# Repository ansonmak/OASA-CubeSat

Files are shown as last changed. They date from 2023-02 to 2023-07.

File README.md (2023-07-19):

# OASA-CubeSat Version 2.1
<p align = "center">
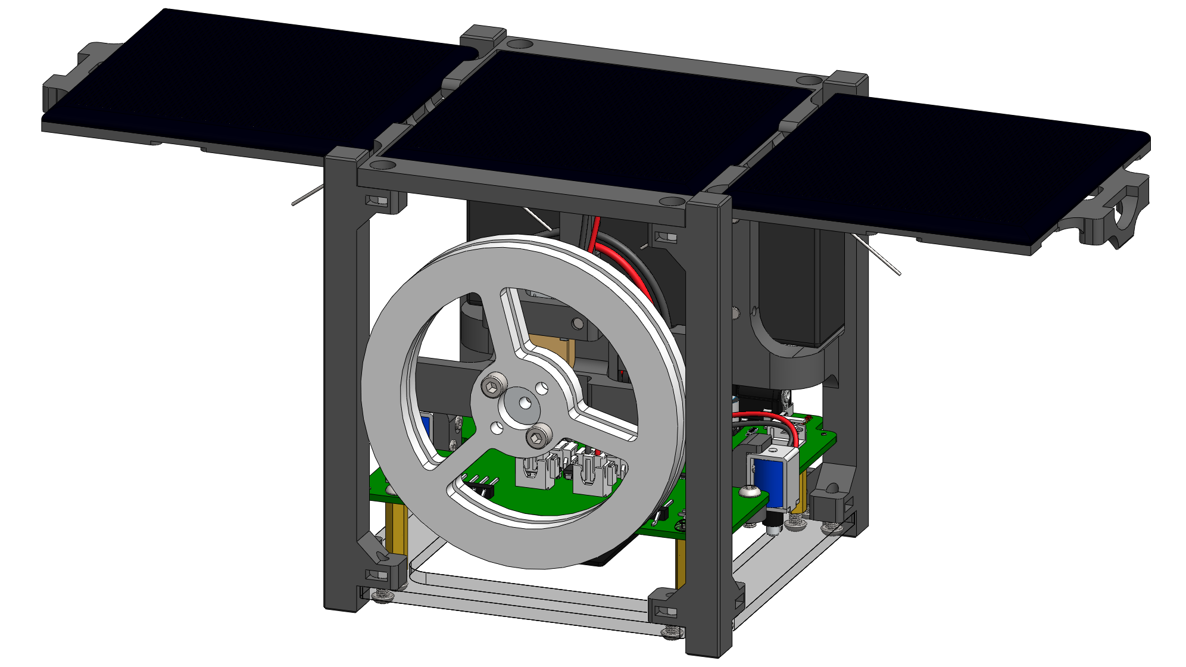
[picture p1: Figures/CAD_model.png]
 
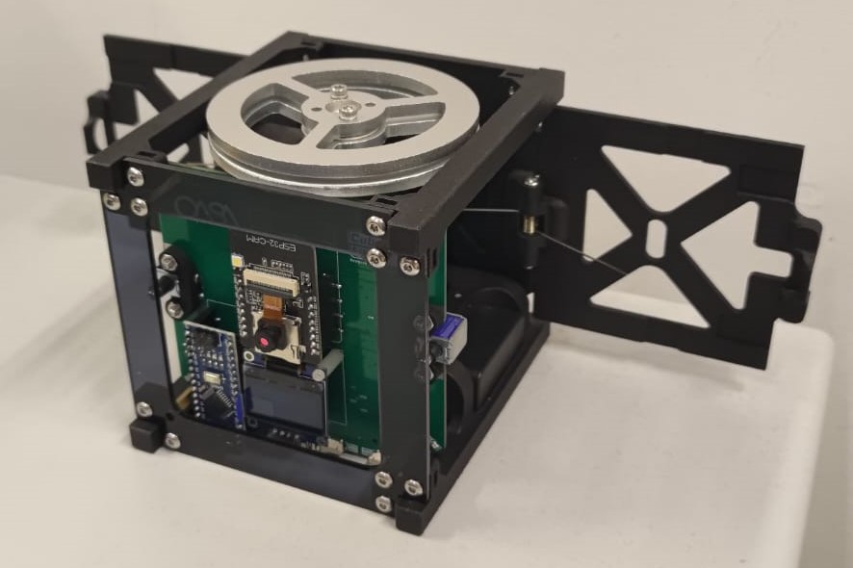
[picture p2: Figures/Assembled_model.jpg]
 
</p>

## 1. Overview
OASA-CubeSat is an educational satellite designed to imitate the most stucture and functions of a CubeSat, which is a cubic miniature satellite with the size of 10x10x10cm. This CubeSat is a double 18650 batteries powered device controlled by two microcontrollers: Arduino Nano and ESP32-CAM. It consists of one 12V geared DC motor for rotating the reaction wheel and two 5V solenoid actuators for deploying the solar panels. The CubeSat also contains a camera with a maximum resolution of 1600 x 1200. With our software uploaded to the microcontrollers, the camera's live-feed is able to transmit to and view it on the PC through its connected WiFi network. The electronics are all connected through our custom PCB mainboard which is attached within the CubeSat’s 3D printed structure.

This repository contains the instructions of how to assemble the CubeSat, guidelines of how to upload the included source code to the CubeSat, and the STL files of the 3D printed parts for replacement of the broken parts or customization.  

## 2. Assembly
Before assembling the CubeSat, check if anything in the kit is missing with the list below: 
- [OASA-CubeSat Kit Checklist](Docs/Checklist.md)

To assemble the CubeSat, follow the instructions below:
- [CubeSat Assembly Instruction](Docs/Assembly.md)

For printing the 3D printed parts with your own printer, check out the STL files in the [`STL`](STL/) to load the 3D models in your slicer.

## 3. Software
The source code of this CubeSat is located in the folder: [`Software`](Software/). Follow the tutorial below to see how to upload the software and operate the CubeSat:
- [Software Upload and CubeSat Operation](Docs/Software.md)

## 4. Copyright
**Copyright © 2023 Orion Astropreneur Space Academy (Hong Kong) Ltd.** 

The intellectual property of this educational CubeSat belongs to Orion Astropreneur Space Academy (Hong Kong) Ltd. All rights reserved.

## 5. Maintenance
For any technical issues, please contact Anson Mak with ansonmak1997@gmail.com.

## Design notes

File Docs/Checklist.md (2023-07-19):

# CubeSat Kit Checklist
- ## Parts
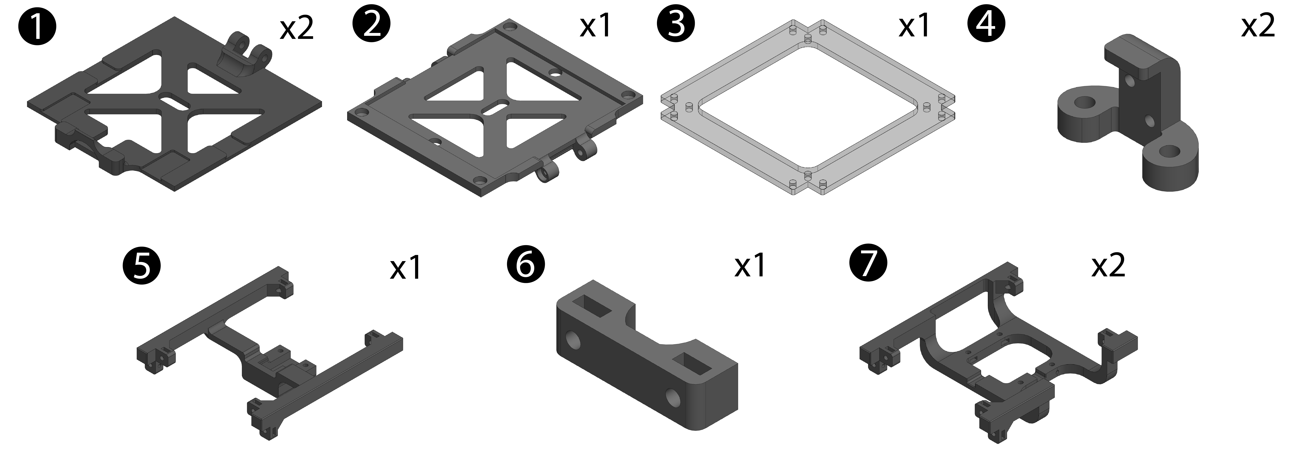
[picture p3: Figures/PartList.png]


- ## Components Box
    - Components of each cell in the box:

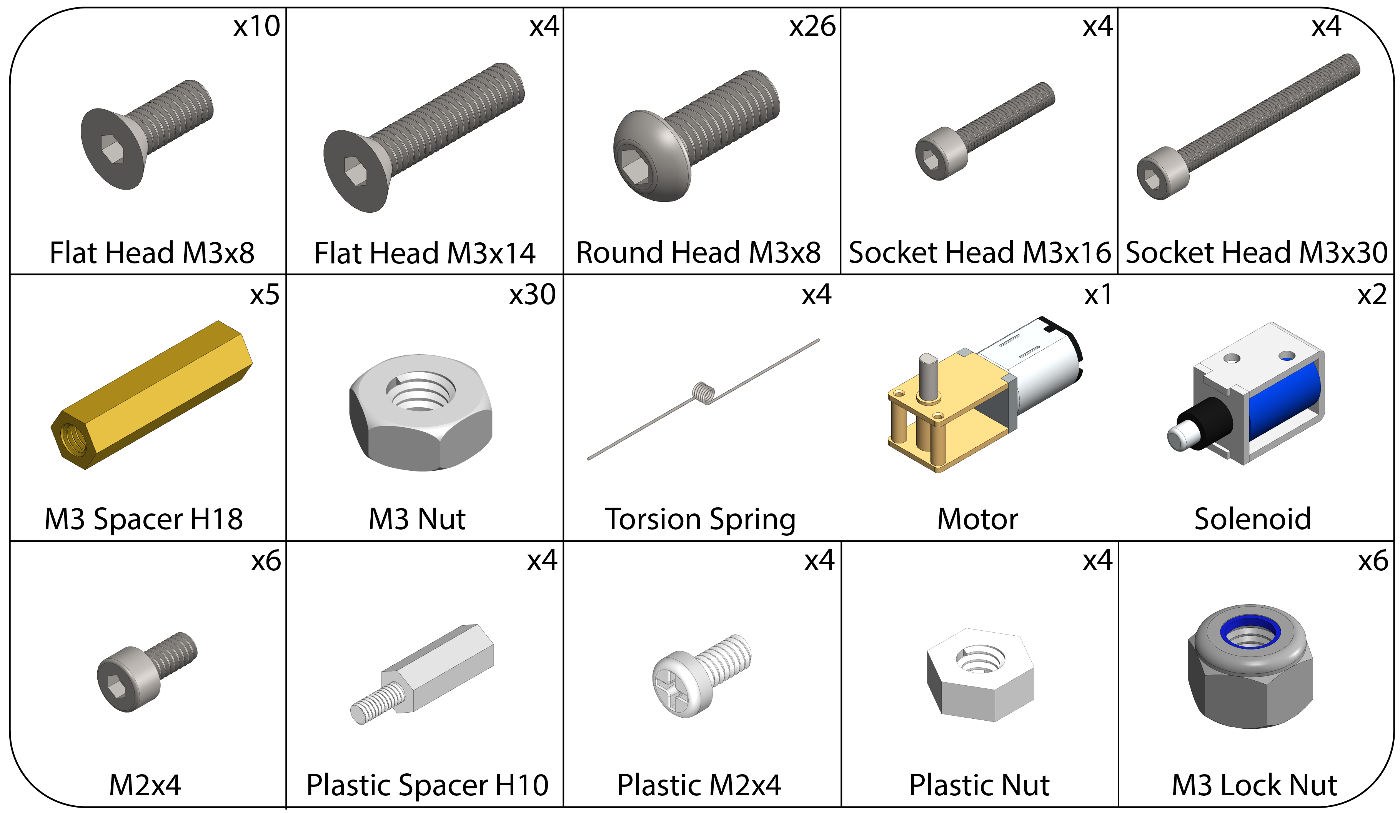
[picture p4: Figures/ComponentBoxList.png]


- ## Electronics
    - ### Mainboard
    - ### ESP32-CAM
    - ### Arduino Nano
    - ### OLED Display

- ## Tools Set
    - ### Hex Key: 1.5mm, 2.0mm, and 2.5mm
    - ### Mini Cross Screwdriver
    - ### Wrench: 5.5mm

- ## Solar Panel x 3

- ## Reaction Wheel Parts

- ## Battery 18650 cell x 2

- ## Battery USB Charger

- ## Battery Power Box

- ## Light Sensor With Wire and Header x 4

- ## Mini USB Wire

- ## Spare 3D Printed Parts

- ## Double Sided Tapes

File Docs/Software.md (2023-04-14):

# Software Tutorial

## 1. Install Arduino IDE
Visit https://www.arduino.cc/en/software to download and install Arduino IDE software on your computer.

## 2. Install ESP32 Board in Arduino IDE
After you have installed Arduino IDE on your computer, you will need to install the ESP32 board library in Arduino IDE before uploading code to the ESP32 board. 

**2.1** Launch Arduino IDE and go to **Files** > **Preferences**.  
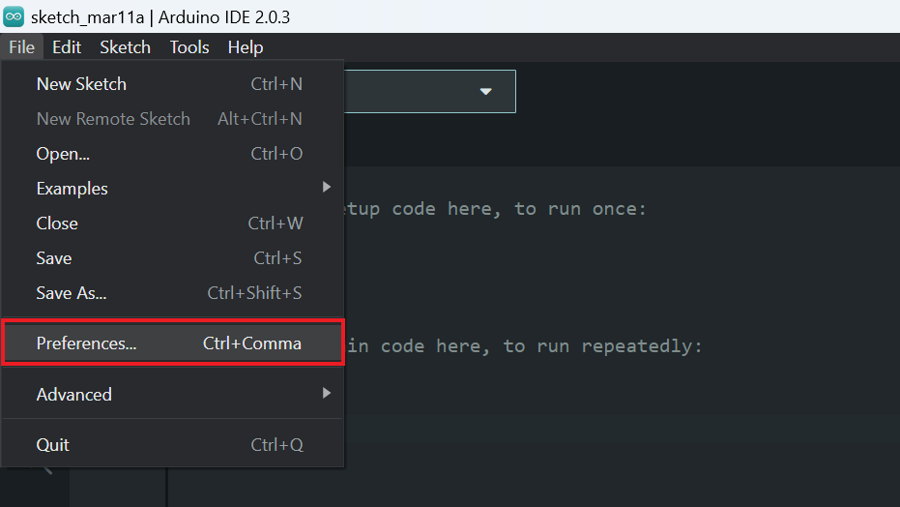
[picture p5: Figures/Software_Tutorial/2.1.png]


**2.2** In **Additional Boards Manager URLs**, paste the following link:
```
https://raw.githubusercontent.com/espressif/arduino-esp32/gh-pages/package_esp32_index.json
```  
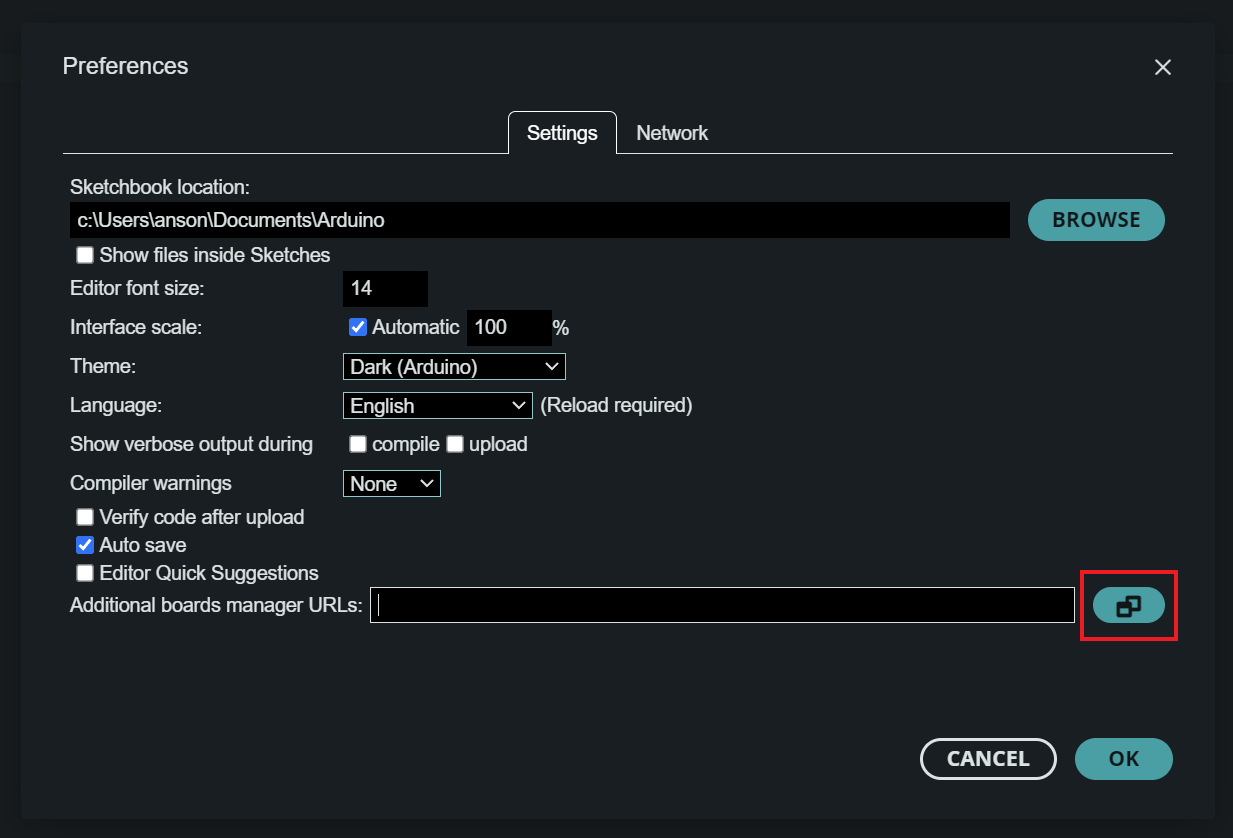
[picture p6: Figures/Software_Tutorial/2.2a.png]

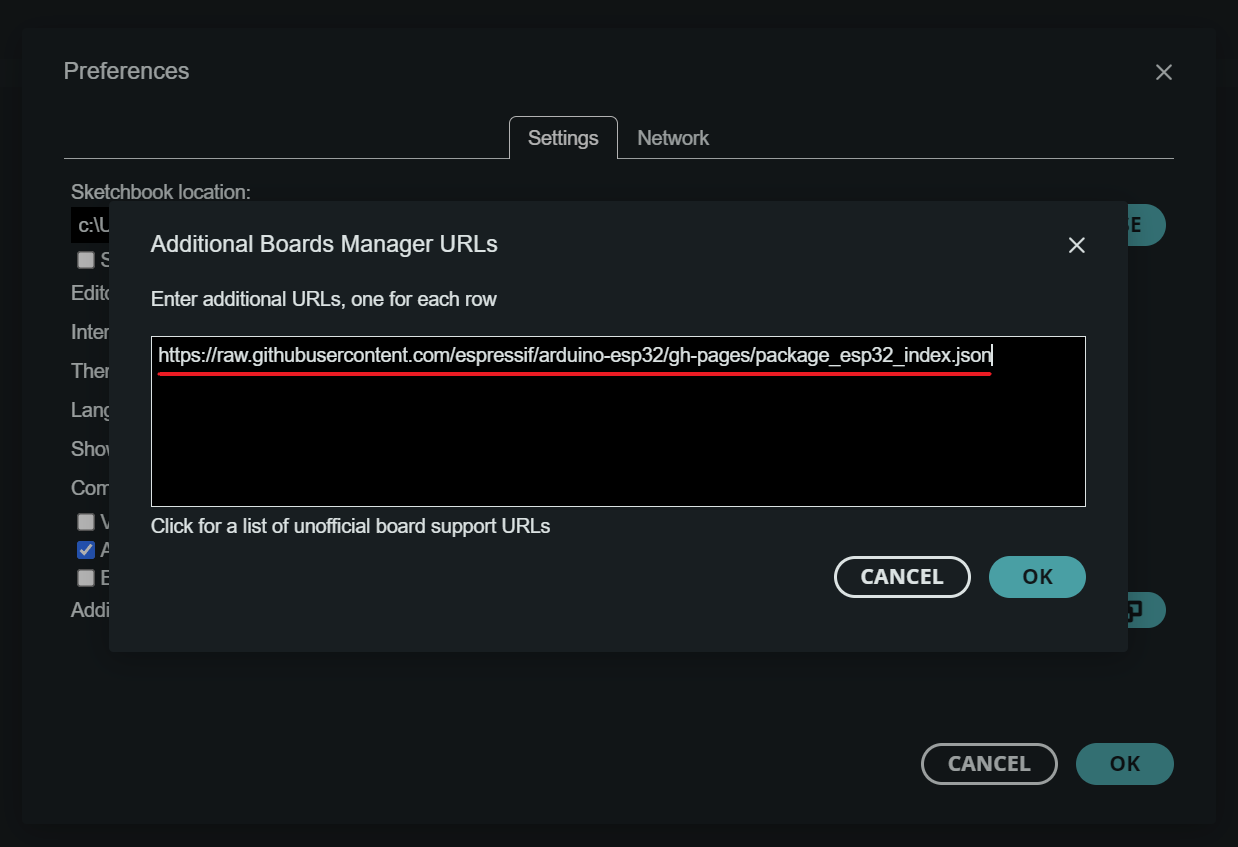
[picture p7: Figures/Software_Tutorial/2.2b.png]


**2.3** In **Tools** > **Board** > **Boards Manager** or click the **Boards Manager** icon on the left bar, search **ESP32** and install with **version 1.0.6**.  
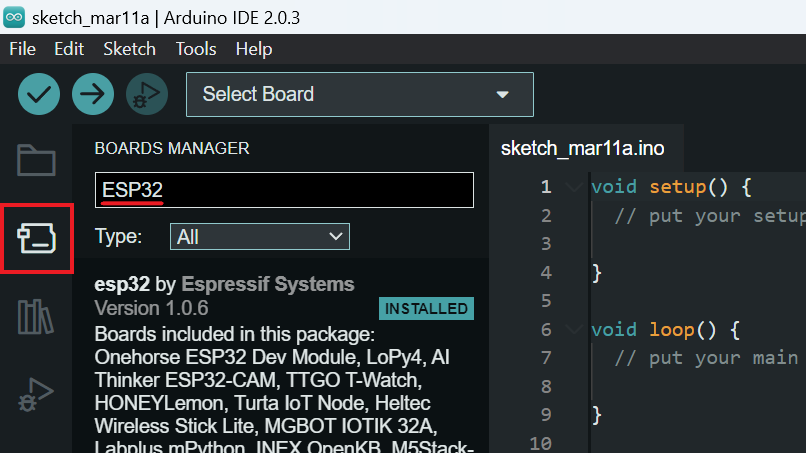
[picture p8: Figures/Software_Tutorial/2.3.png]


## 3. Install Libraries in Arduino IDE
In **Tools** > **Manage Libraries...** or click the **Library Manager** icon on the left bar, install the following three libraries with the latest version.
- **3.1** **WiFiManager** by *tzapu*  
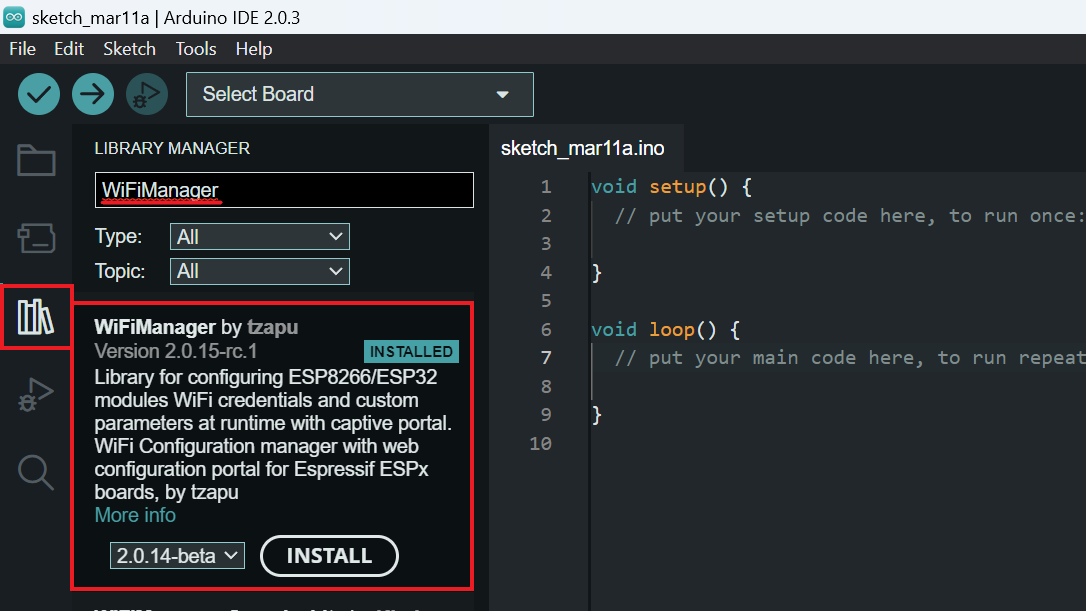
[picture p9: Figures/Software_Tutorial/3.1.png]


- **3.2** **Adafruit SSD1306** by *Adafruit*  
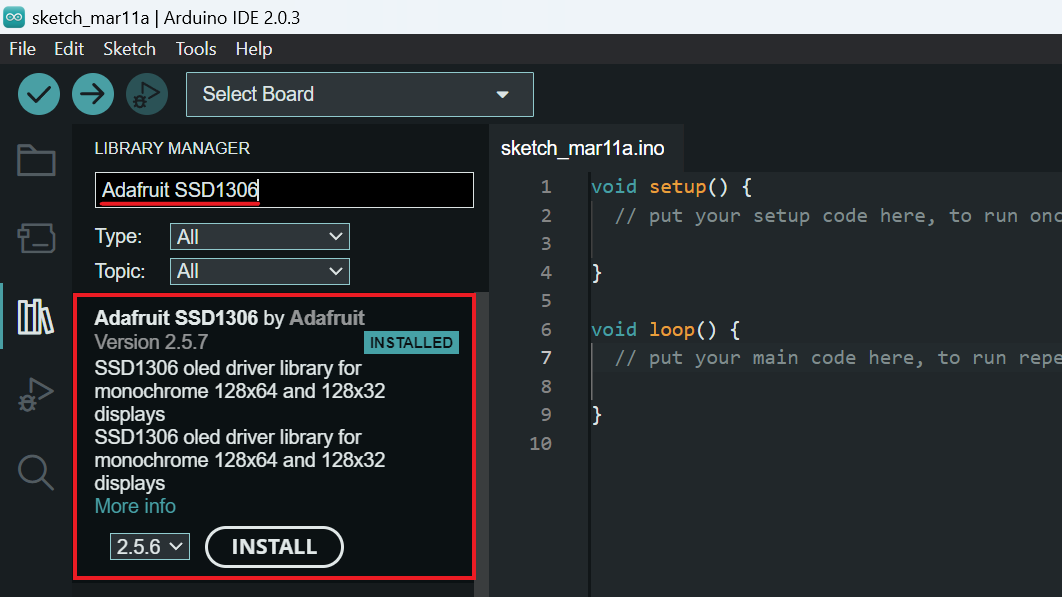
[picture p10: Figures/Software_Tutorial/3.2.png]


- **3.3** **Adafruit GFX Library** by *Adafruit*  
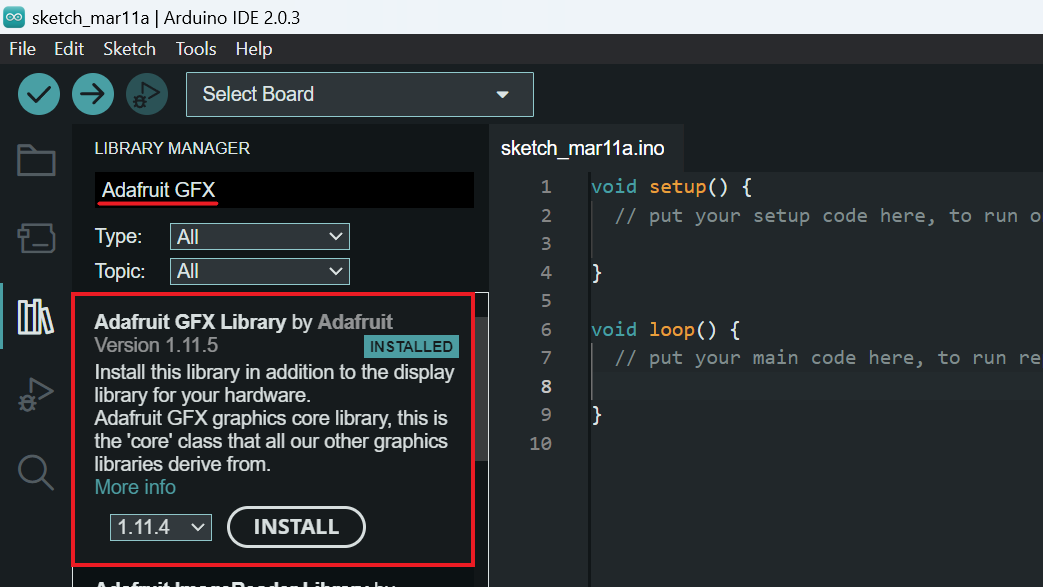
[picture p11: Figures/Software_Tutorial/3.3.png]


## 4. Upload Code to ESP32-CAM
**4.1** Open the file [`ESP32-CAM.ino`](../Software/ESP32-CAM/ESP32-CAM.ino) in the folder [`Software/ESP32-CAM`](../Software/ESP32-CAM/) with Arduino IDE.

**4.2** Turn off the CubeSat by sliding the power switch on the battery box to the **OFF** side.  
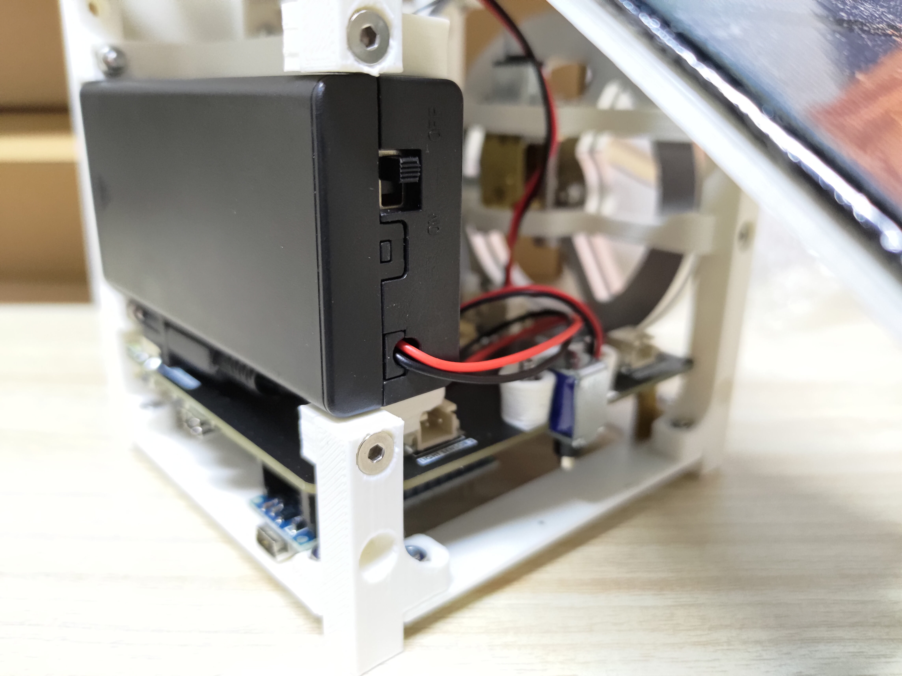
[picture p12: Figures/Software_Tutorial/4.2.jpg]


**4.3** Plug in the mini USB wire to the mainboard and connect to your PC.  
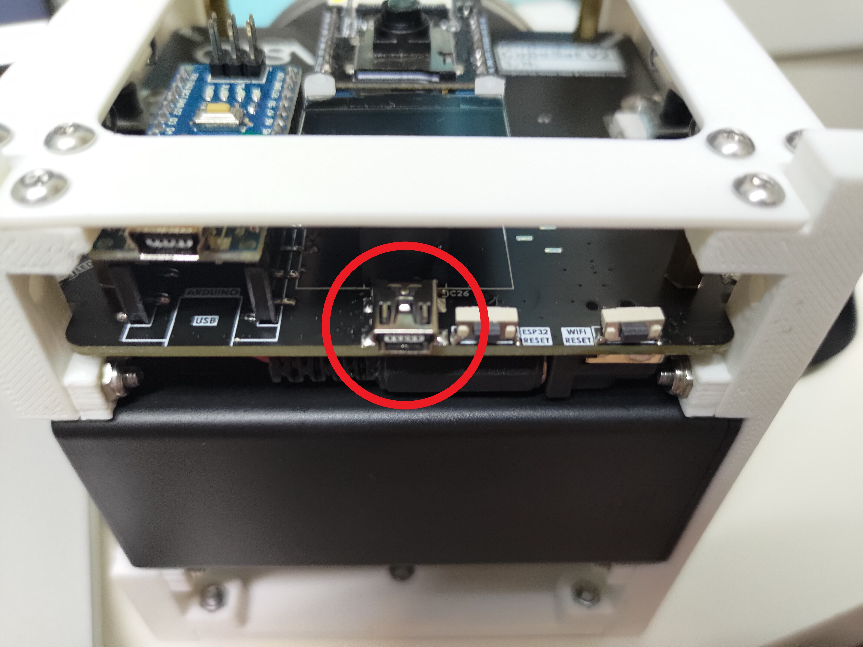
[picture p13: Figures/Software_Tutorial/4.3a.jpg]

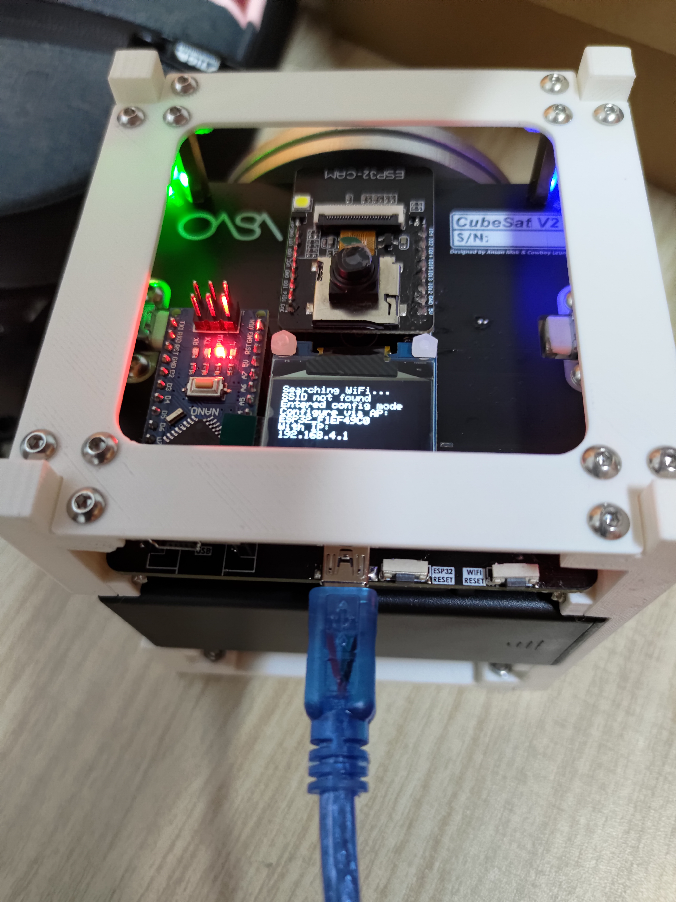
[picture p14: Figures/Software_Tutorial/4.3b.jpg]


**4.4** In your Arduino IDE, go to **Tools** > **Board** > **esp32** > select **ESP32 Wrover Module**.  
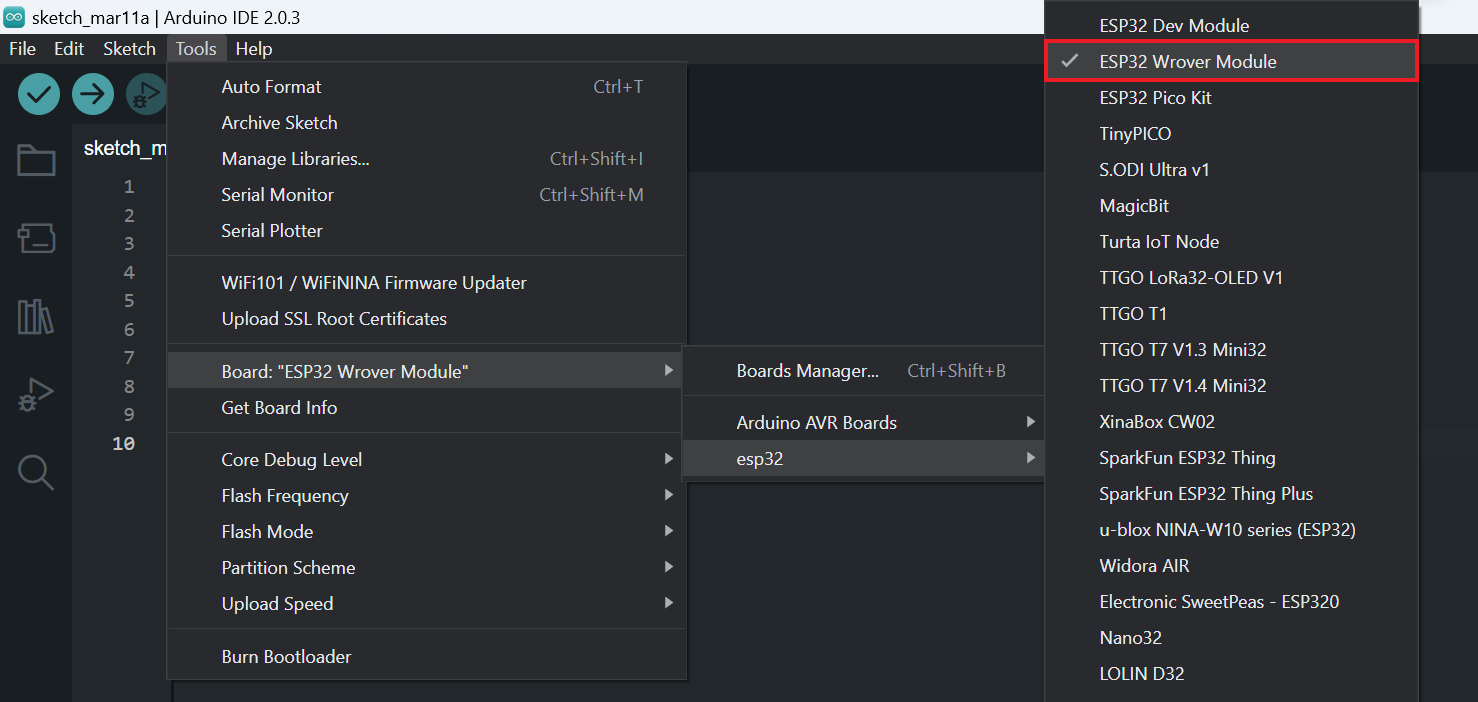
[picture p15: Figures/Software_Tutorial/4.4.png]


**4.5** In **Tools**, select the upload configuration as follows:
- **Port**: COMX (Try different COM port one by one if multiple COM ports appear)
- **Core Debug Level**: None
- **Flash Frequency**: 80MHz
- **Flash Mode**: QIO
- **Partition Scheme**: Huge App (3MB No OTA)
- **Upload Speed**: 921600

**4.6** Click the **Upload** arrow icon on the top left corner to start compile and upload the code to ESP32-CAM.  
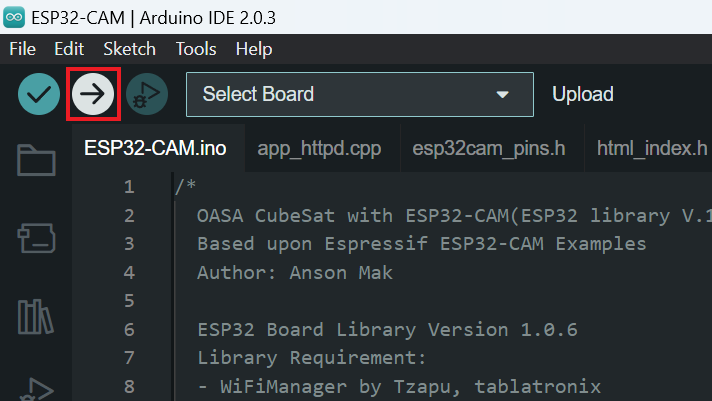
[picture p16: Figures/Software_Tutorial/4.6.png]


During uploading, the message ***"Writing at 0x00000000... (xx%)"*** will be shown up in the **Output** window at the botton of Arduino IDE.  
***Please do not unplug the USB wire during this process.***

If the message ***"Leaving... Hard resetting via RIS Pin..."*** shows up, the upload is completed and the Mini USB wire can be unplugged.

## 5. Upload Code to Arduino Nano
**5.1** Plug the Mini USB connected to your PC to Arduino Nano.  
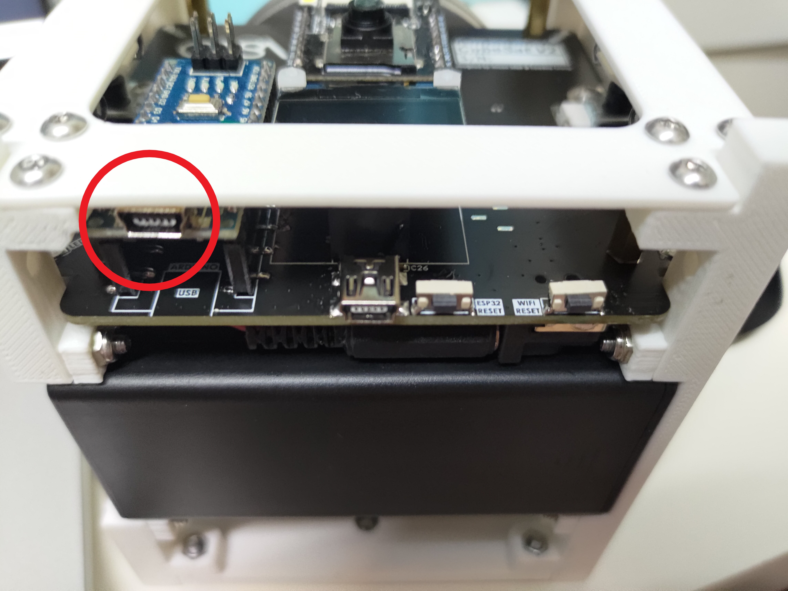
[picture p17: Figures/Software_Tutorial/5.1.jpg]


**5.2** In **Tools** > **Board** > **Arduino AVR Boards** > select **Arduino Nano**.  
In  **Tools** > **Processor** > select **ATmega328P (Old Bootloader)**.  (If the upload failed, try different processor since the processor varies across different manufracturers.)  
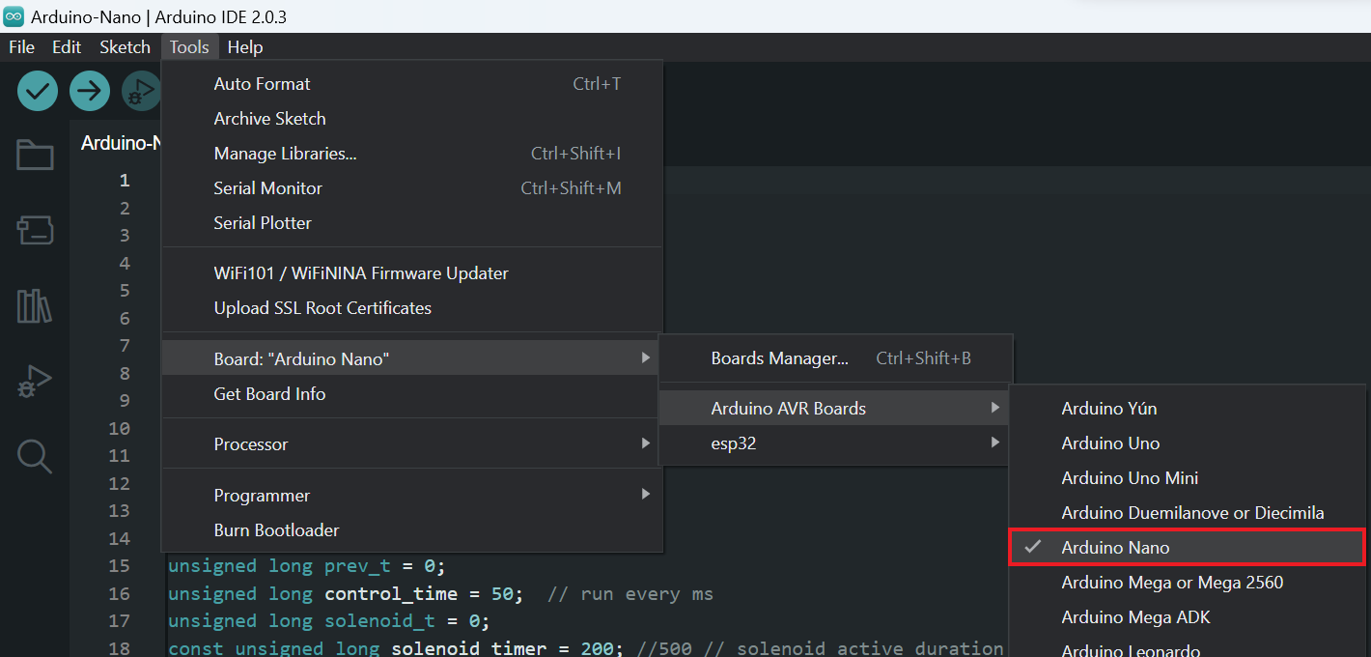
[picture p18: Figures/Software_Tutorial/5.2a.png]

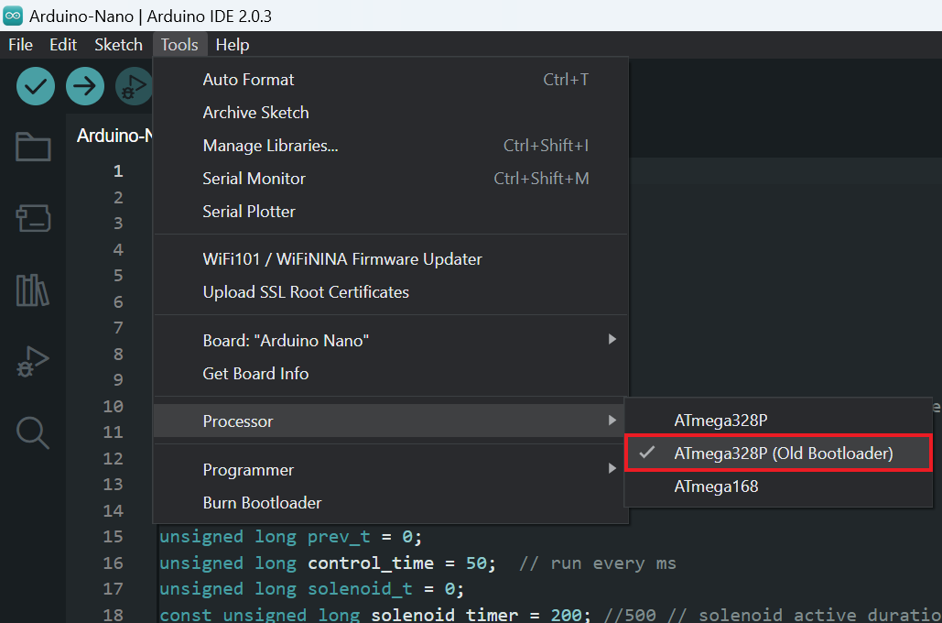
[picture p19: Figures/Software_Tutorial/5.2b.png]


**5.3** Click the **Upload** arrow icon on the top left corner to start compile and upload the code.  
If completed, the message ***"Done Uploading"***  will be shown and the Mini USB wire can be unplugged.

## 6. Power the CubeSat and Connect to WiFi
**6.1** Turn on the power switch by sliding the switch to the **ON** side. If the OLED doesn't show up any message, press the **ESP reset** button.
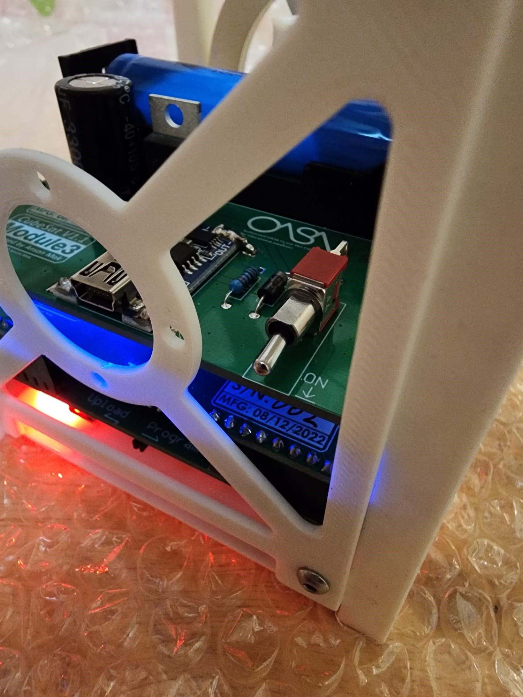
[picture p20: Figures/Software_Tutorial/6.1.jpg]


**6.2** The message ***"Searching WiFi..."*** will be shown on the OLED diplay and the ESP32-CAM will search for the saved WiFi credentials in the board, which is the SSID and the password of a hotspot.  
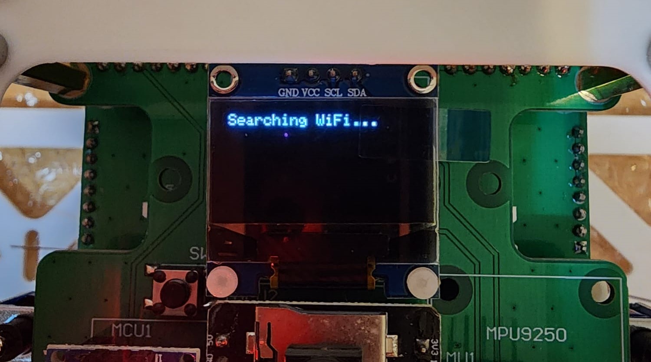
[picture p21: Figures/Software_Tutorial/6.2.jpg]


**6.3** If the LED on the ESP32-CAM will flash multiple times, the ESP32-CAM is connected to the WiFi network and its IP adress will be shown on the display.  
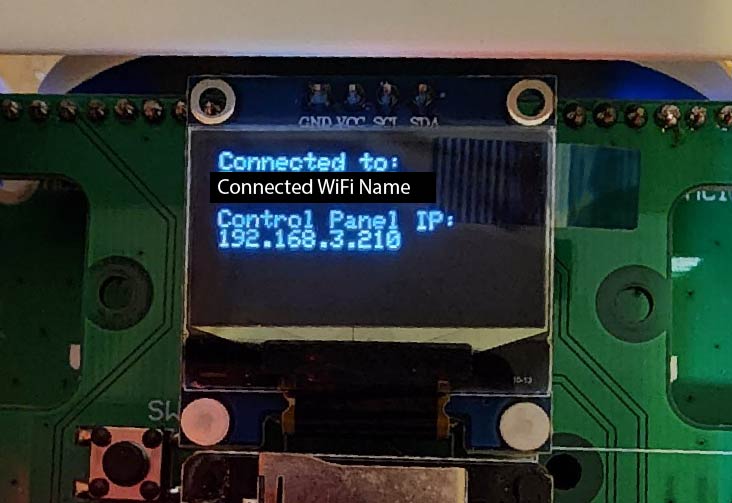
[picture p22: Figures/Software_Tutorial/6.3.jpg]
  
If the message ***"SSID not found. Entered config mode."*** is shown on the display, the ESP32-CAM cannot found its saved WiFi network. See ***Sec. 6.5*** for changing its WiFi configurations.

**6.4** Connect your device (PC, laptop, mobile phone, or tablet) to the same WiFi network that the CubeSat is connected to. Open the browser and search with the IP address. A web page of CubeSat's control panel will be shown.  Go to ***Sec. 7*** to see how to control the CubeSat.  
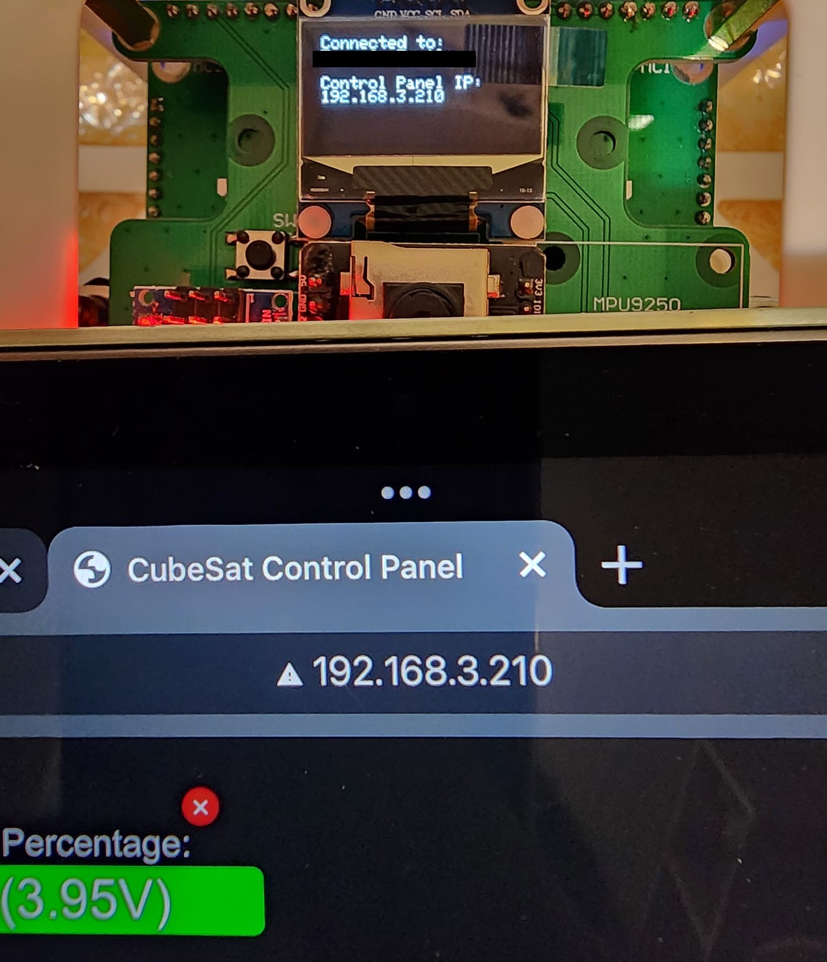
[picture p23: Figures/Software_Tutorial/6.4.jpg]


**6.5** If the saved WiFi credentials is not found, the CubeSat will turn into **Config mode** and display its SSID name on the OLED display.  
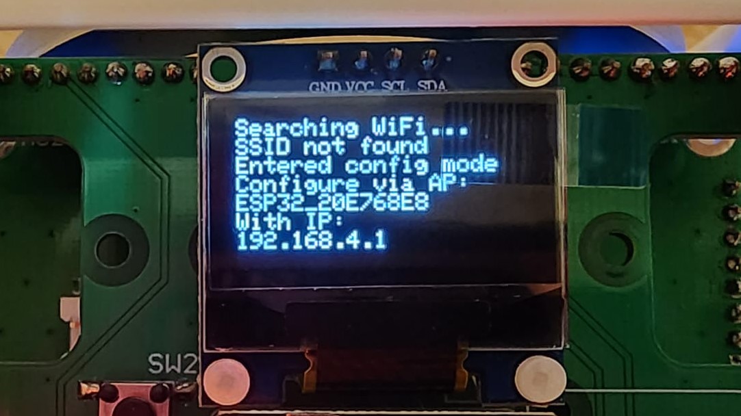
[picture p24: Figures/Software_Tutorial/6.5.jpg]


**6.6** Use any device with WiFi connectivity to search SSID name of the CubeSat.  
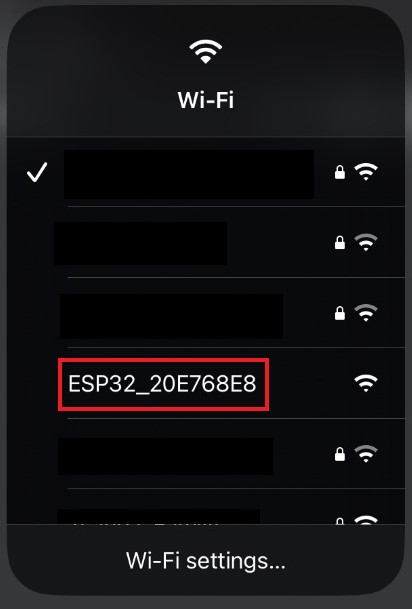
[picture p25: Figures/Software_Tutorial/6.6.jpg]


**6.7** After your device is connected to the CubeSat through the SSID, the **WiFi Manager** page will show up on your device. Click **configure WiFi** > select the WiFi network that you want your CubeSat to connect or type the SSID and password in the box below.  
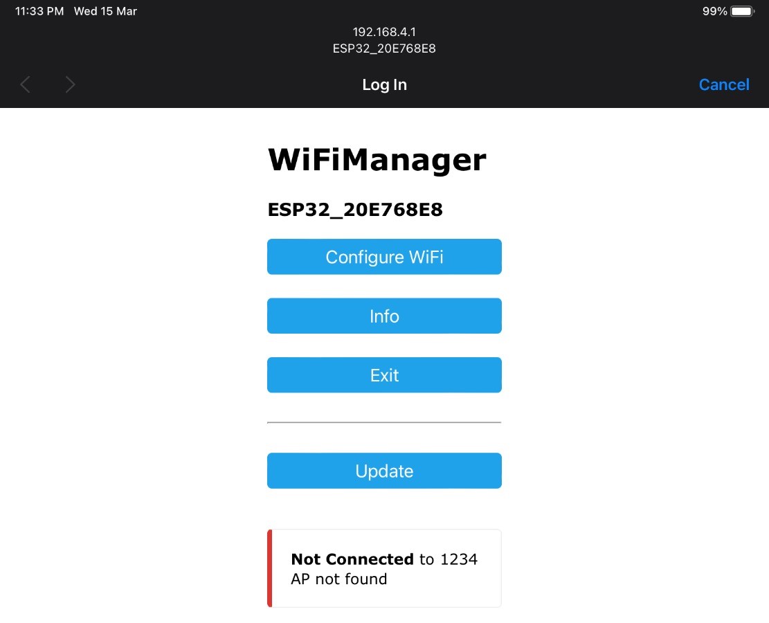
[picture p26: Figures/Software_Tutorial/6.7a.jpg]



**6.8** Click save and close the **WiFi Manager** page on your device. Turn off power of your CubeSat and turn on again to reset. Repeat ***Sec. 6.1*** to try the new WiFi connection.

**6.9** If you want to erase the saved WiFi credentials to reconfigure the WiFi settings, you can press the hold the **WiFi Reset** button while pressing the **ESP Reset** button once. This can force the ESP32-CAM entering the **Config mode**.  


## 7. Control the CubeSat Remotely with the Control Panel
After the successful WiFi connection, a control panel shown below can be access by searching the CubeSat's IP address on the browser.  


**7.1** **Camera Live Stream**  
Press the green **Start Stream** button to start the video stream. Press the red **Rotate Stream** button to rotate the video image if the orientation is wrong. The two sliding bar below are used to increase video resolution and video quilty.

**7.2** **Solar Panel Deploy**  
The **Deploy** button is used to release the spring-loaded solar panels by activating the solenoids. 

**7.3** **Reaction Wheel Control**  
The third sliding bar is used to control the motor coupled to the reaction wheel. Drag the slider to control the motor rotate left and right. Press the **Stop Motor** button below to stop the motor.

**7.4** **Light Sensor Readings**  
The CubeSat has four ports to install the light sensors. They are located at the left and right sides after the solar panels deployed.  

  
After plugging the light sensors to the ports, the readings will be shown on the control panel.  
  

**7.5** **Battery Meter**  
The top left green bar is the battery meter. The four LEDs on the mainboard are also showing the battery percentage: 
- 4 LEDs ON: 75-100%
- 3 LEDs ON: 50-75%
- 2 LEDs ON: 25-50%
- 1 LED ON: 0-25%. ***Need Charging: take out the batteries and put it in the charger.***

  

**7.6** **CubeSat LED Flash**  
The **Flash LED** button will flash the LED located on the ESP32-CAM.

**7.7** **Auto Light Tracking**  
The **Light Tracking** button will turn on an auto light tracking mode by comparing the light sensors values located at the left and right side. The CubeSat will rotate the reaction wheel to change its orientation for facing its solar panels to the brightest direction.

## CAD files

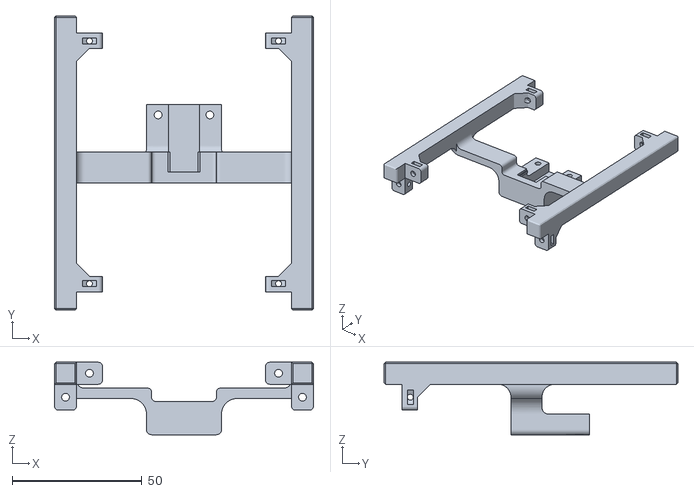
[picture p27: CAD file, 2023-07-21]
STL/5_FrontFrame.STL
100.0 x 113.5 x 28.0

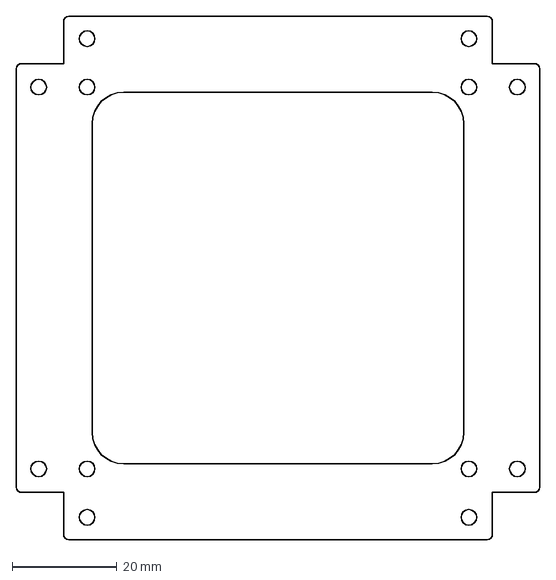
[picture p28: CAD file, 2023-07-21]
STL/3_BottomPanel.DXF
100.0 x 100.0 mm

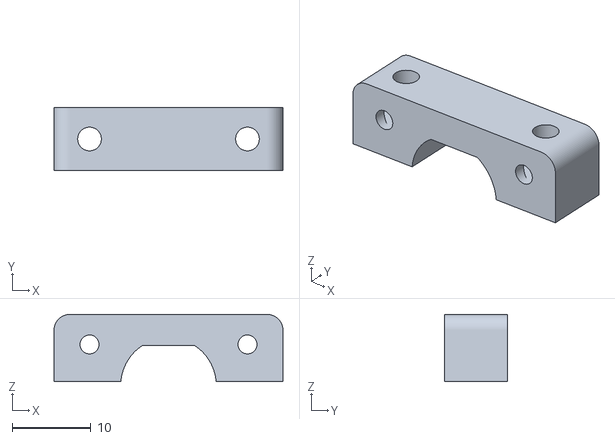
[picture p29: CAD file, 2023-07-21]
STL/6_MotorTopMount.STL
29.0 x 8.00 x 8.50

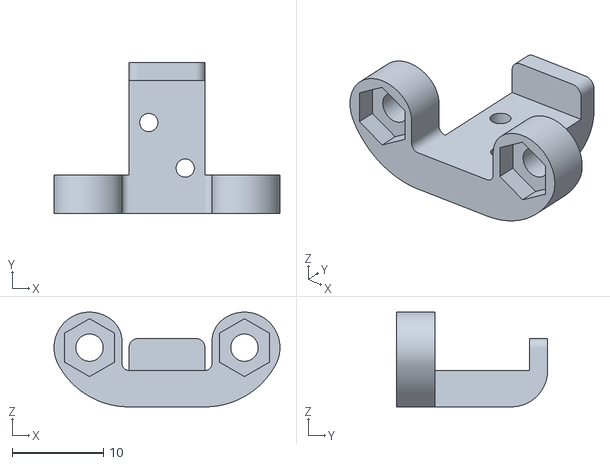
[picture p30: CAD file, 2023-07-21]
STL/4_SolenoidPCBMount.STL
24.8 x 16.6 x 10.4

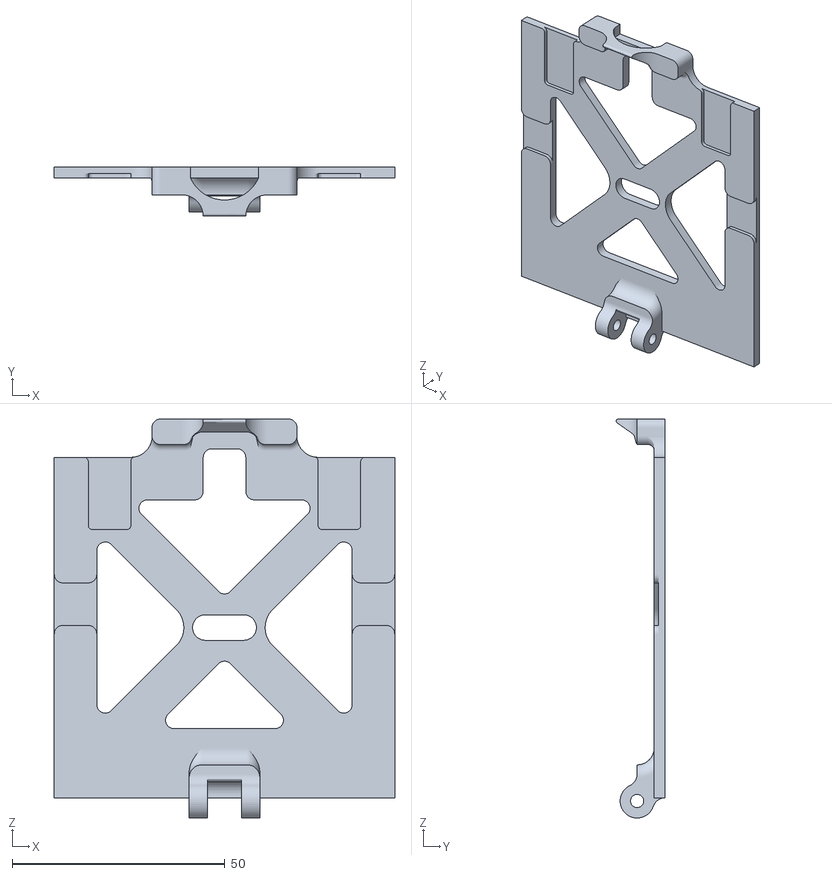
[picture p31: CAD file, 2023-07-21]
STL/1_DeployPanel.STL
80.0 x 11.4 x 93.7

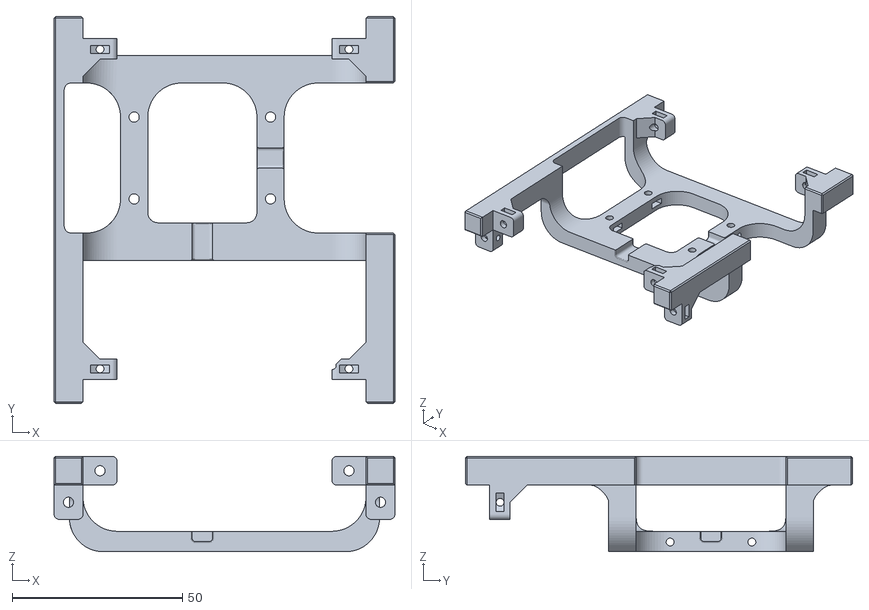
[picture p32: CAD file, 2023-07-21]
STL/7_BackFrame.STL
100.0 x 113.5 x 28.0

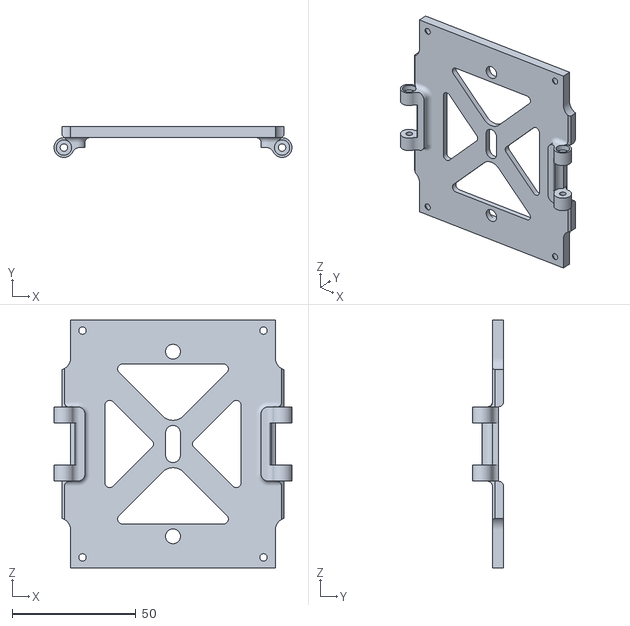
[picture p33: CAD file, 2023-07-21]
STL/2_TopPanel.STL
96.0 x 12.5 x 100.0

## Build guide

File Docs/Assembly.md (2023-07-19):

# CubeSat Assembly Instructions

## Step 1
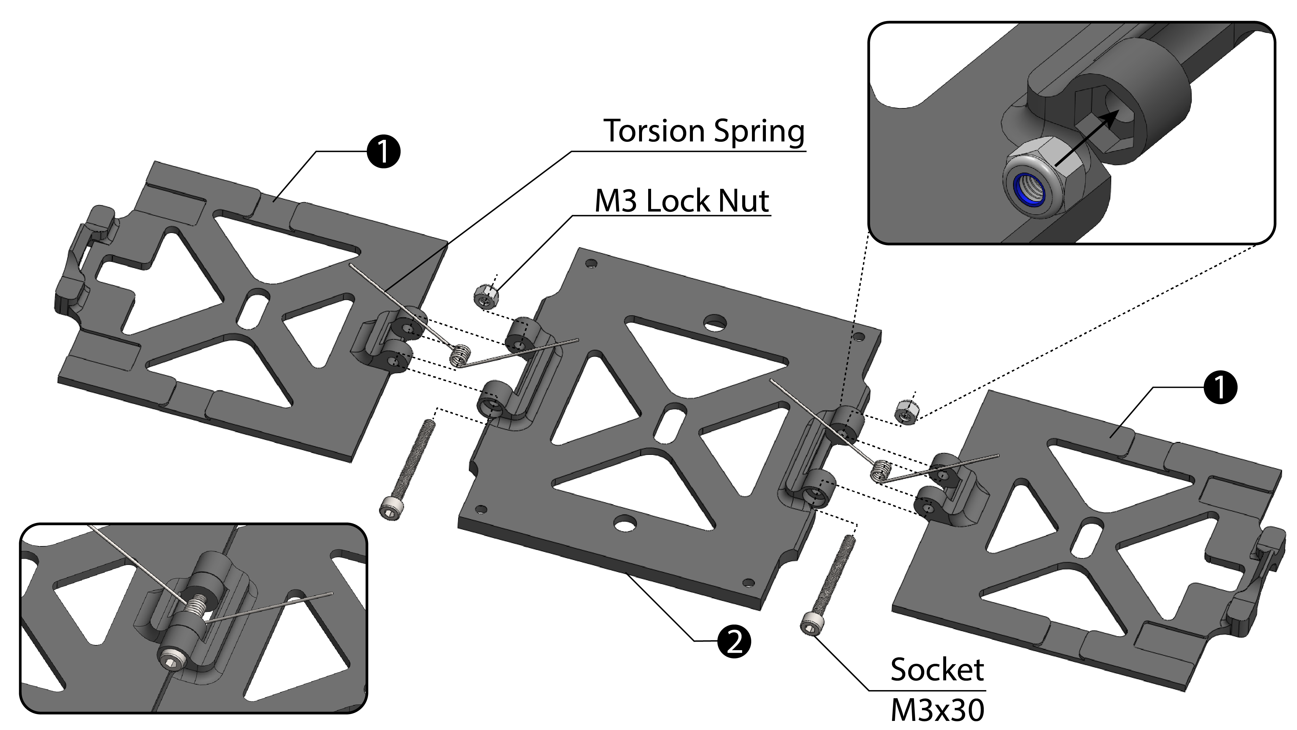
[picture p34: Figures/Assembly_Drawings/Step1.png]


## Step 2
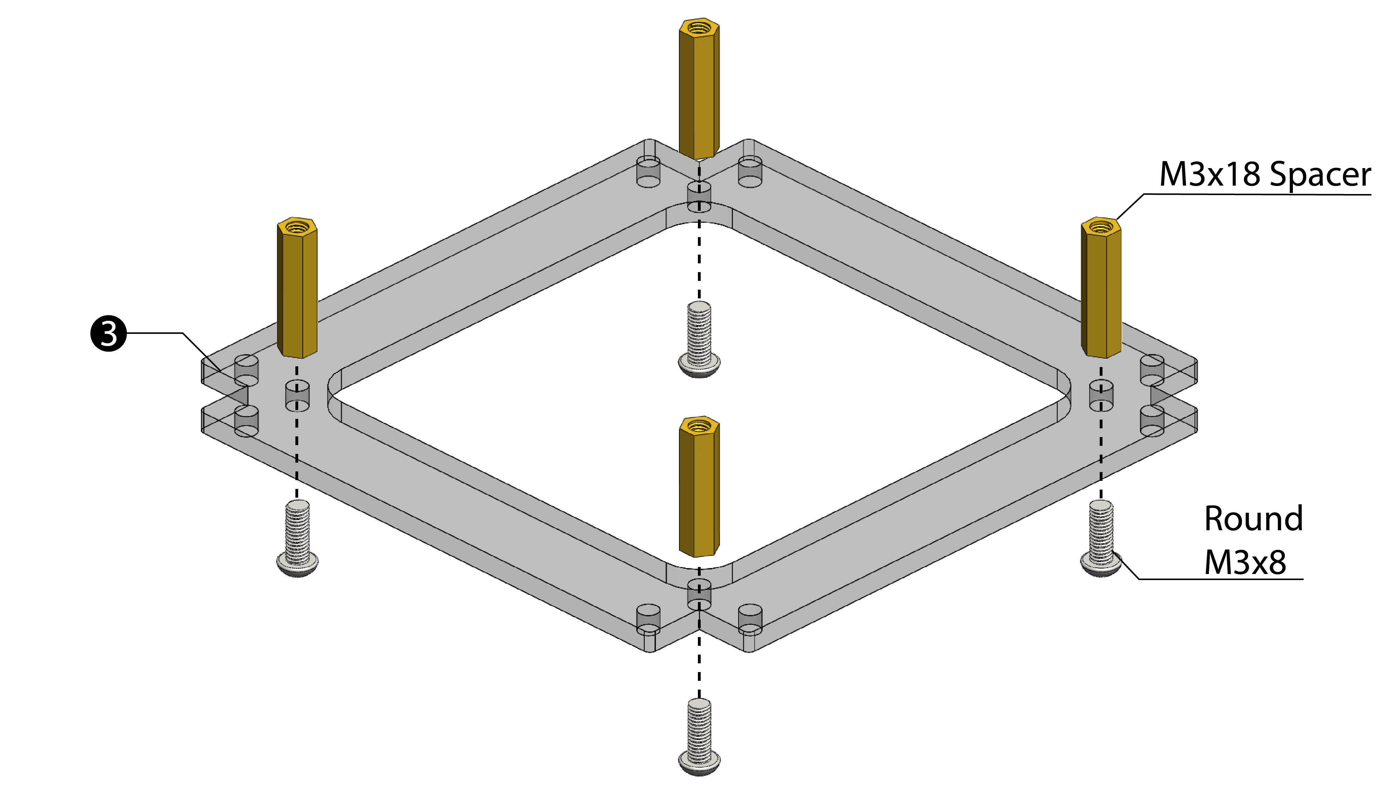
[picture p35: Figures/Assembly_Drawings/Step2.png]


## Step 3
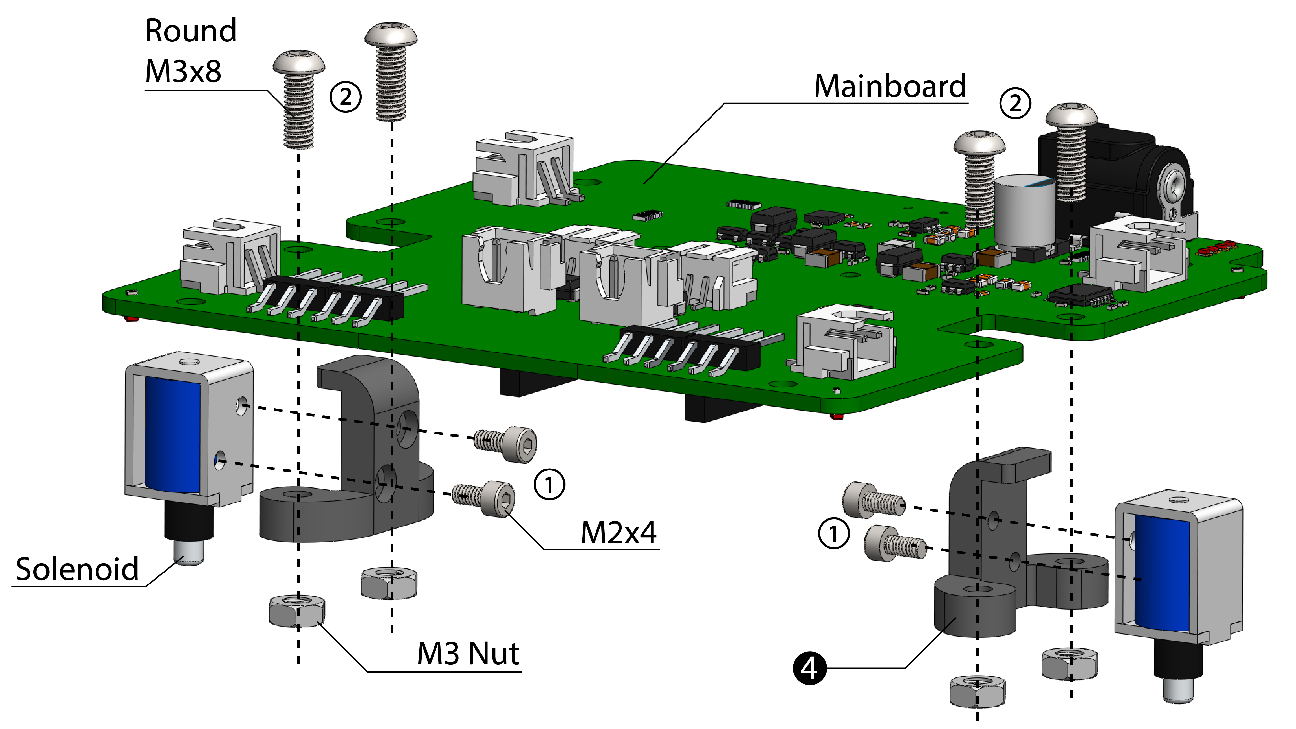
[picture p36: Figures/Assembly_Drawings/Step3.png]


## Step 4
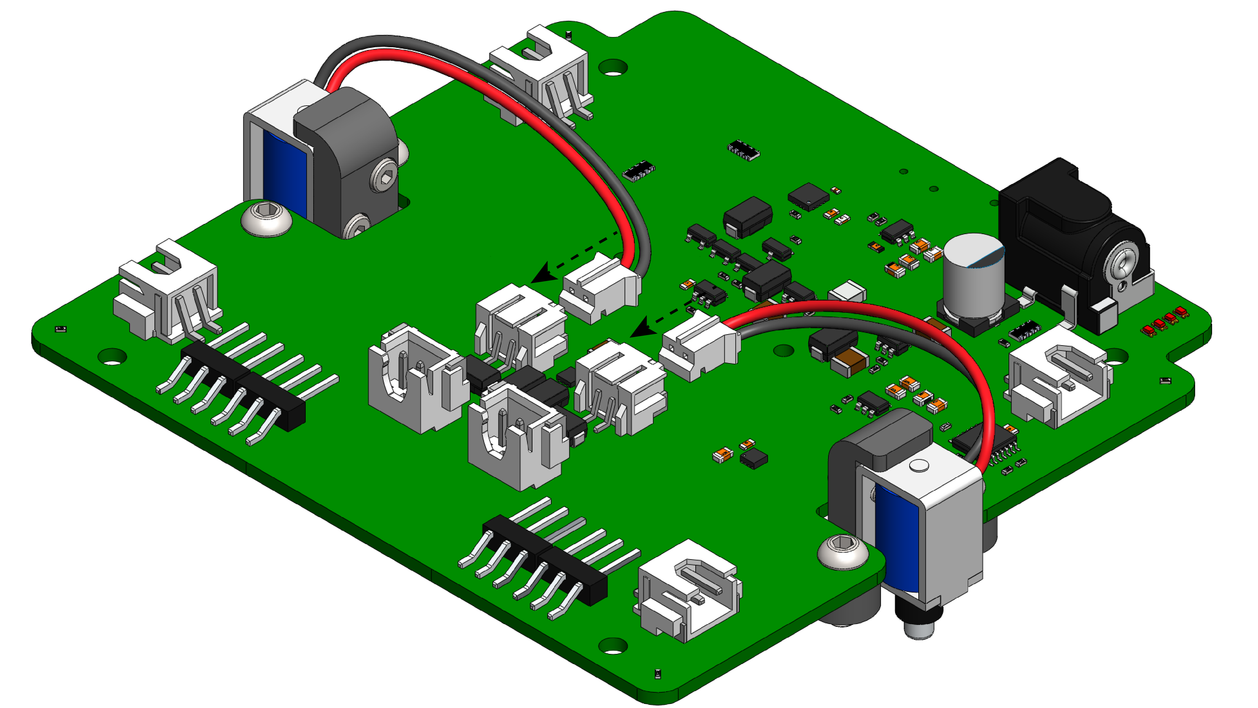
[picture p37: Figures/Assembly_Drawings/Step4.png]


## Step 5
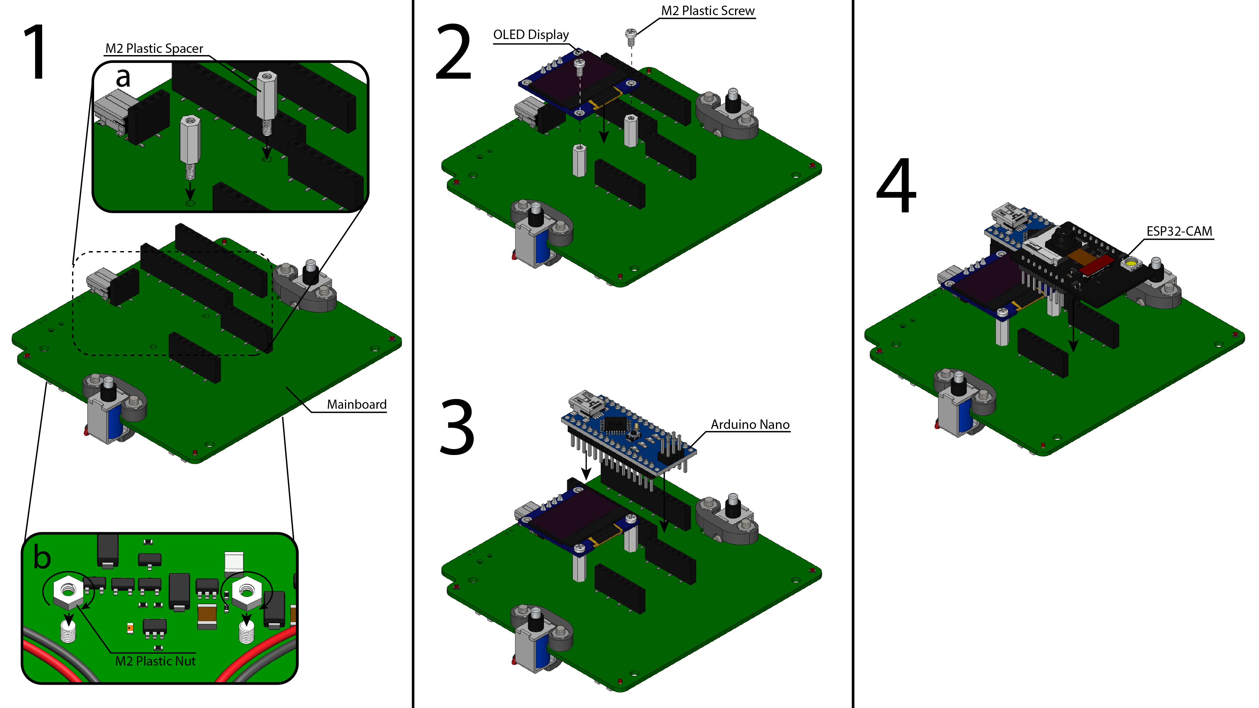
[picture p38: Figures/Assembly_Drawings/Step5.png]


## Step 6
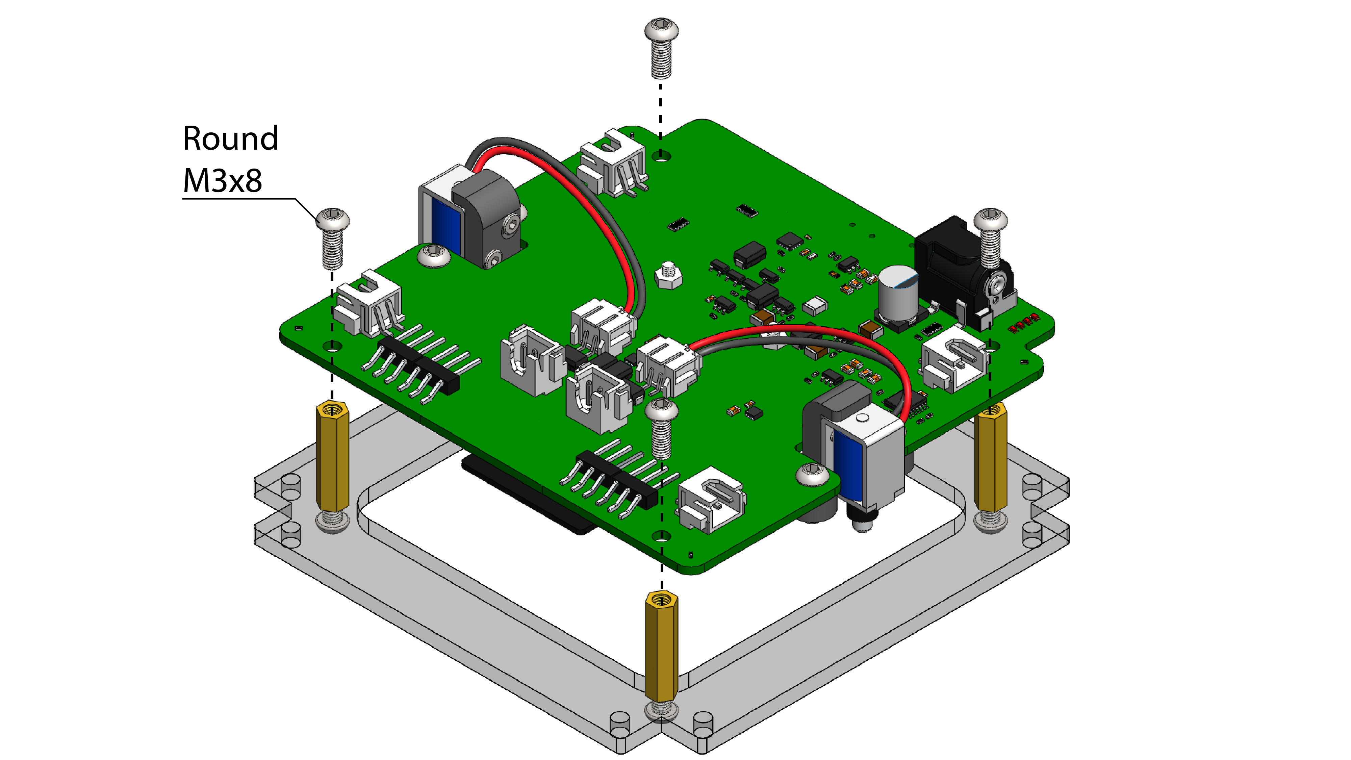
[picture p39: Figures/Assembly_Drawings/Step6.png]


## Step 7
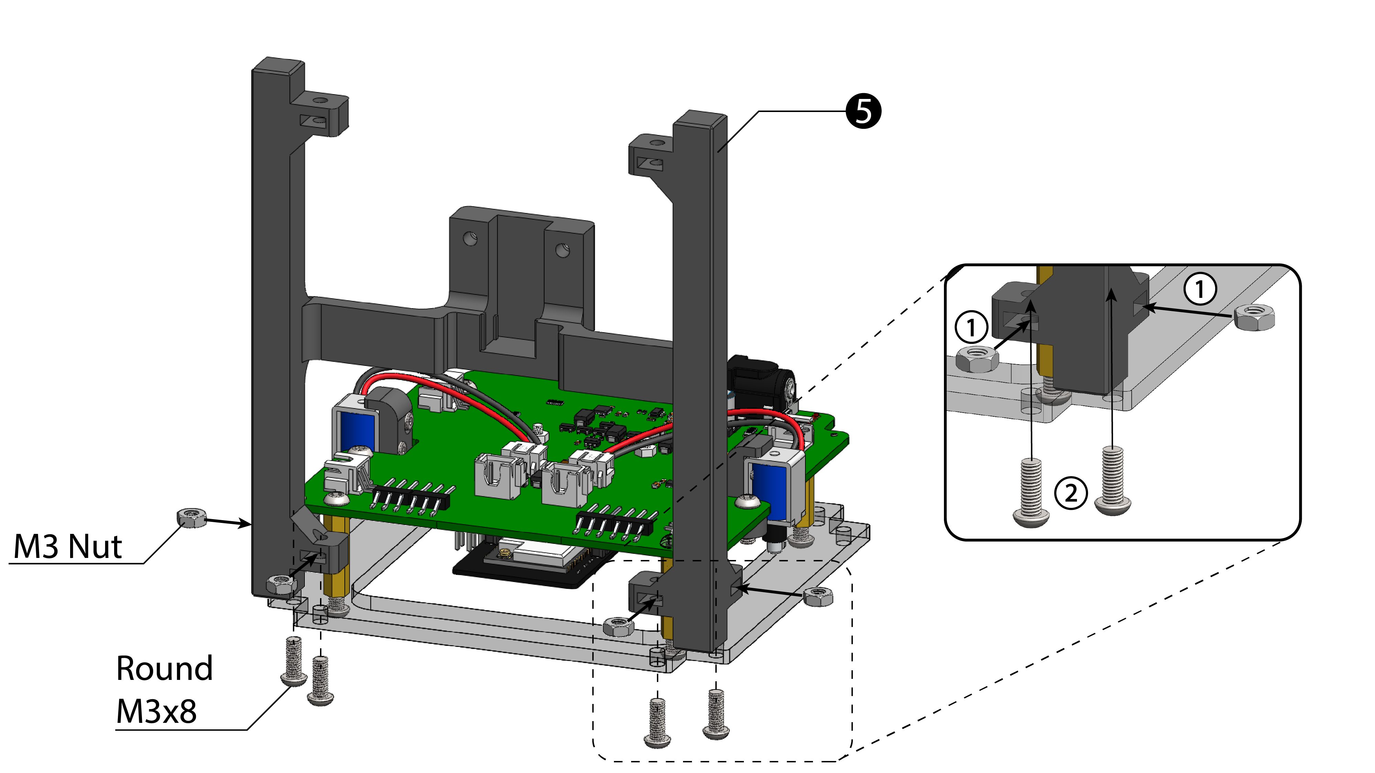
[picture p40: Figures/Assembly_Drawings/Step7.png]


## Step 8
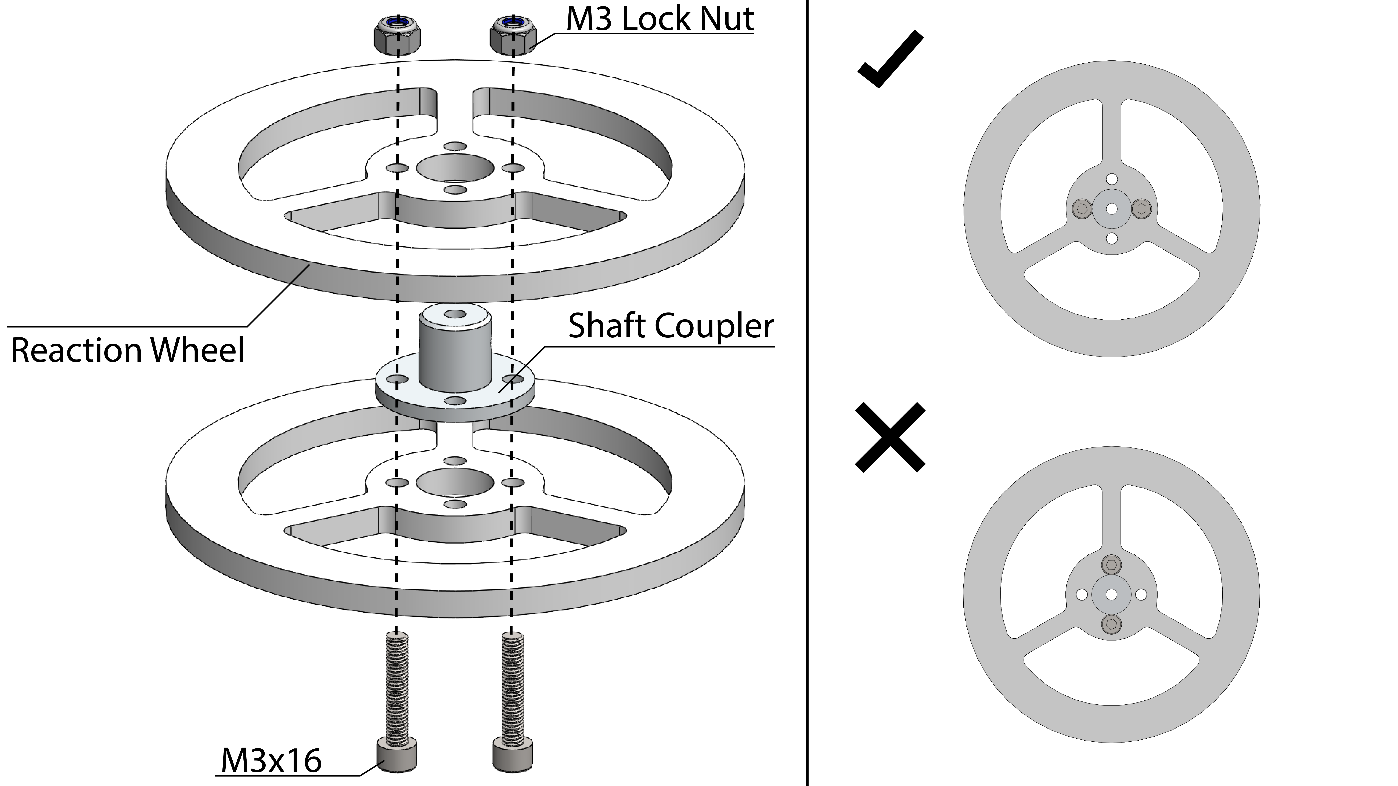
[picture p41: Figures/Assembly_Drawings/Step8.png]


## Step 9
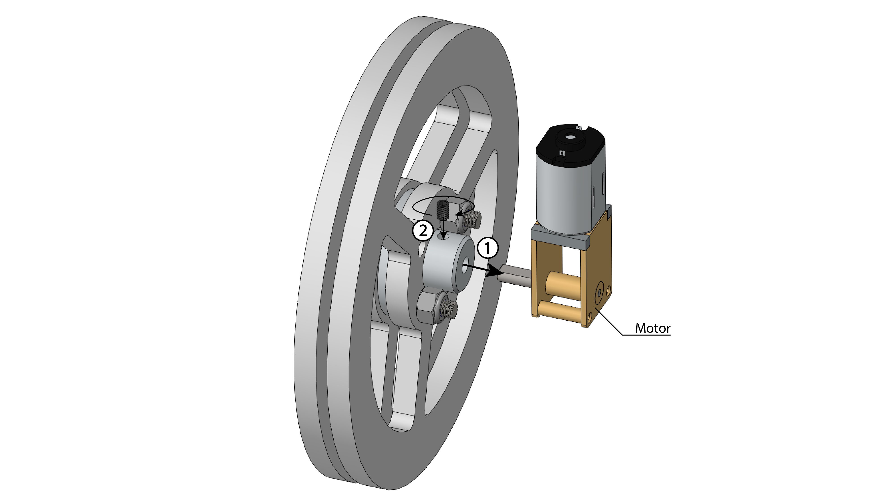
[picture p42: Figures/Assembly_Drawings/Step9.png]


## Step 10
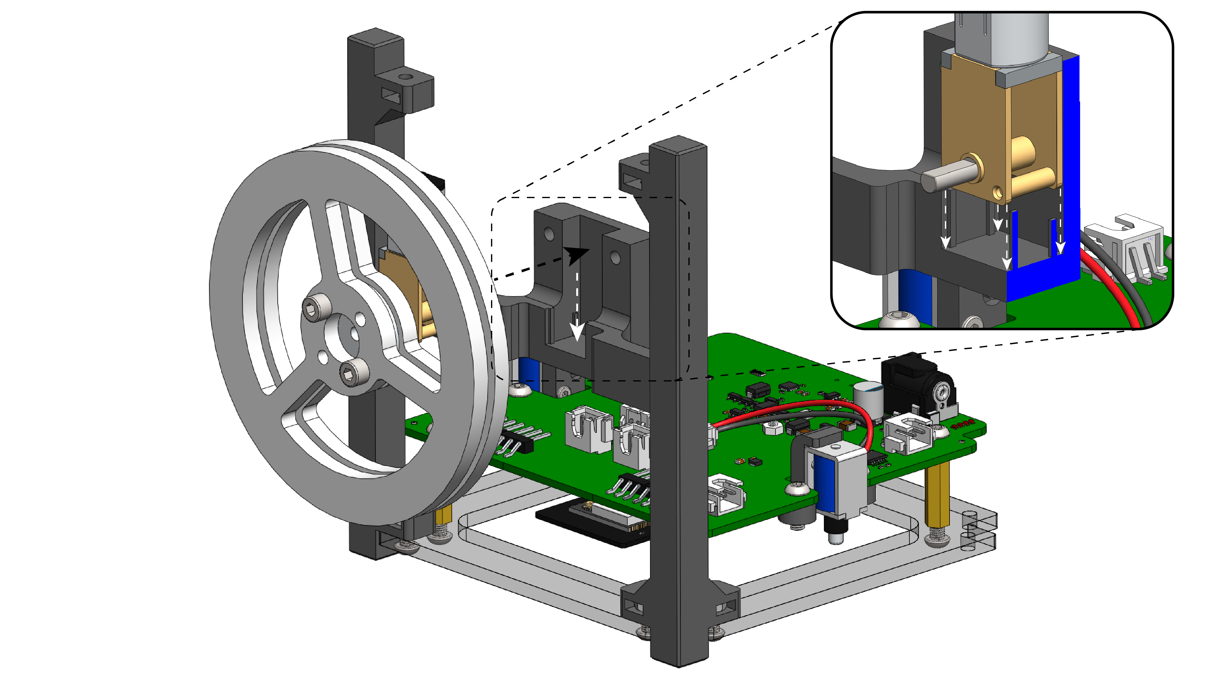
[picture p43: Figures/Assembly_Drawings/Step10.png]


## Step 11
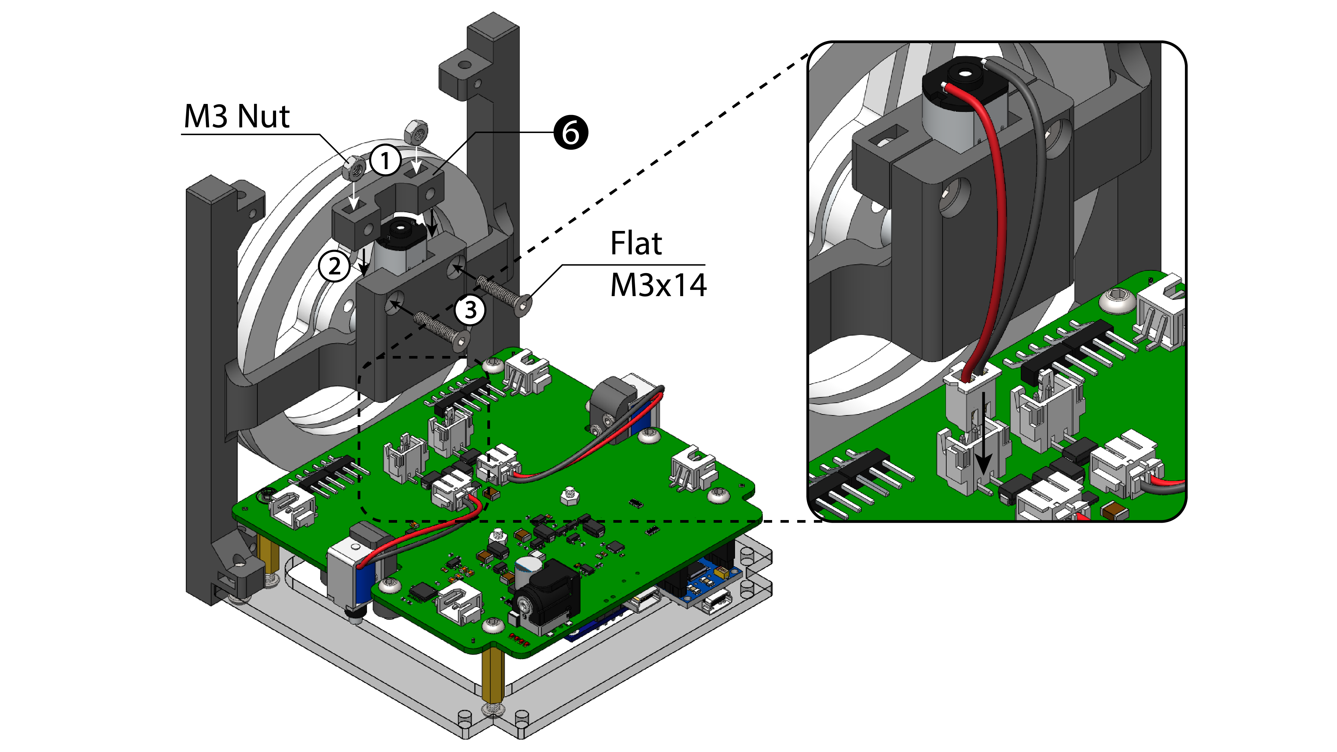
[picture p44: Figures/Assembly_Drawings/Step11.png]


## Step 12
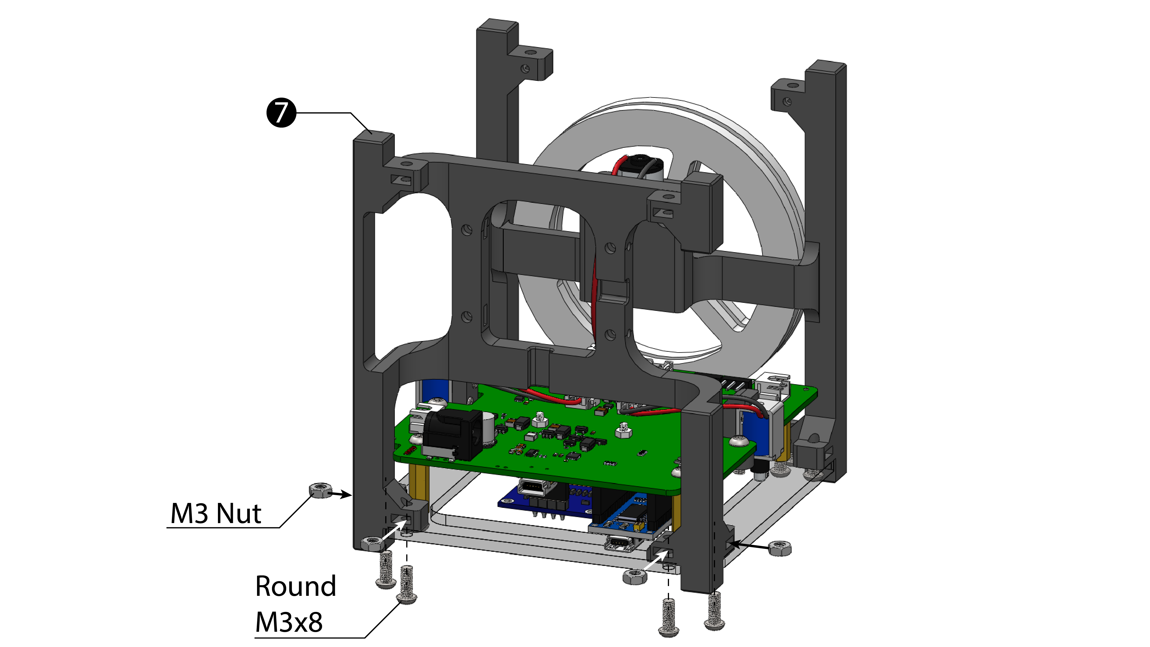
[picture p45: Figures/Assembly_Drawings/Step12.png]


## Step 13
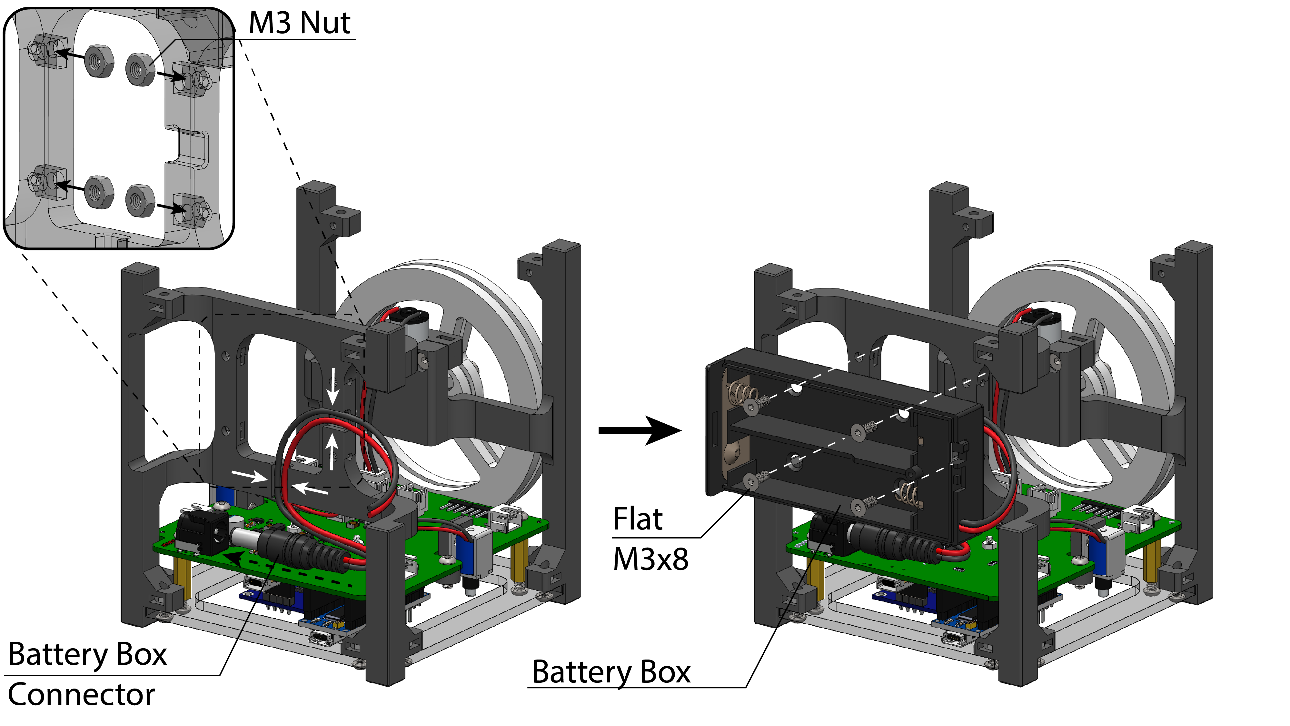
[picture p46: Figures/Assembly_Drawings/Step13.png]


## Step 14
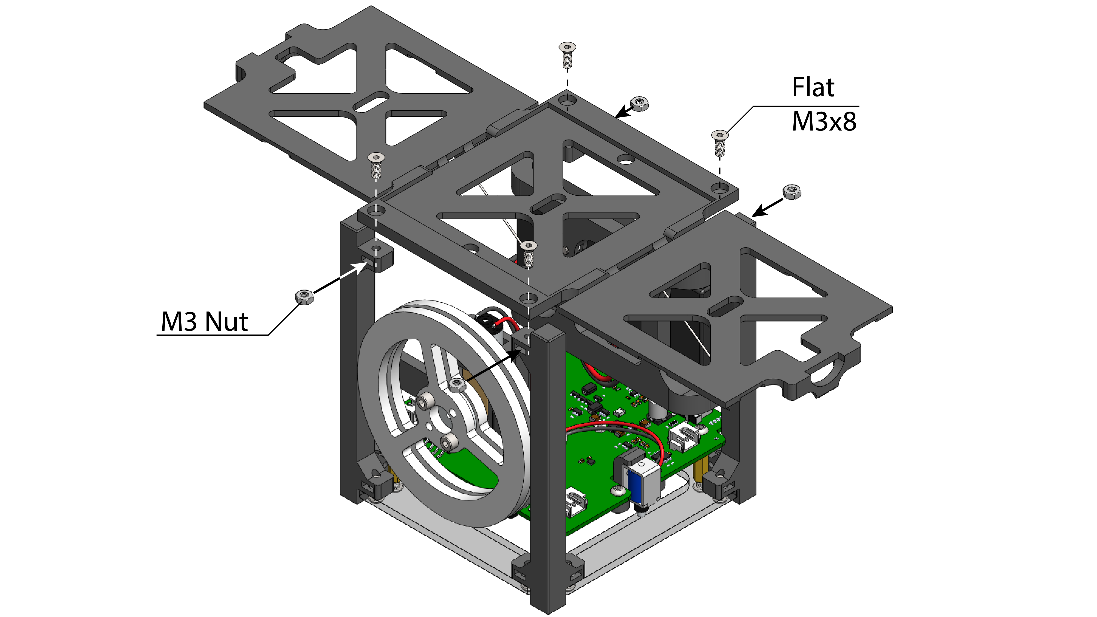
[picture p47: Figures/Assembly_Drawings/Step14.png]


## Step 15
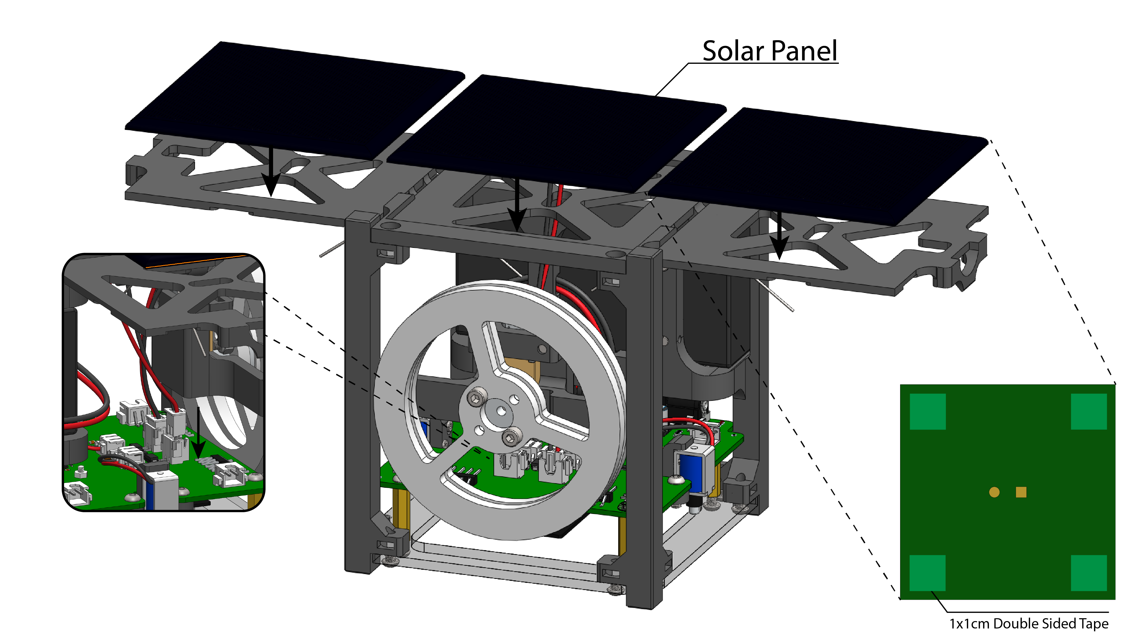
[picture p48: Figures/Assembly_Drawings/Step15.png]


## Step 16
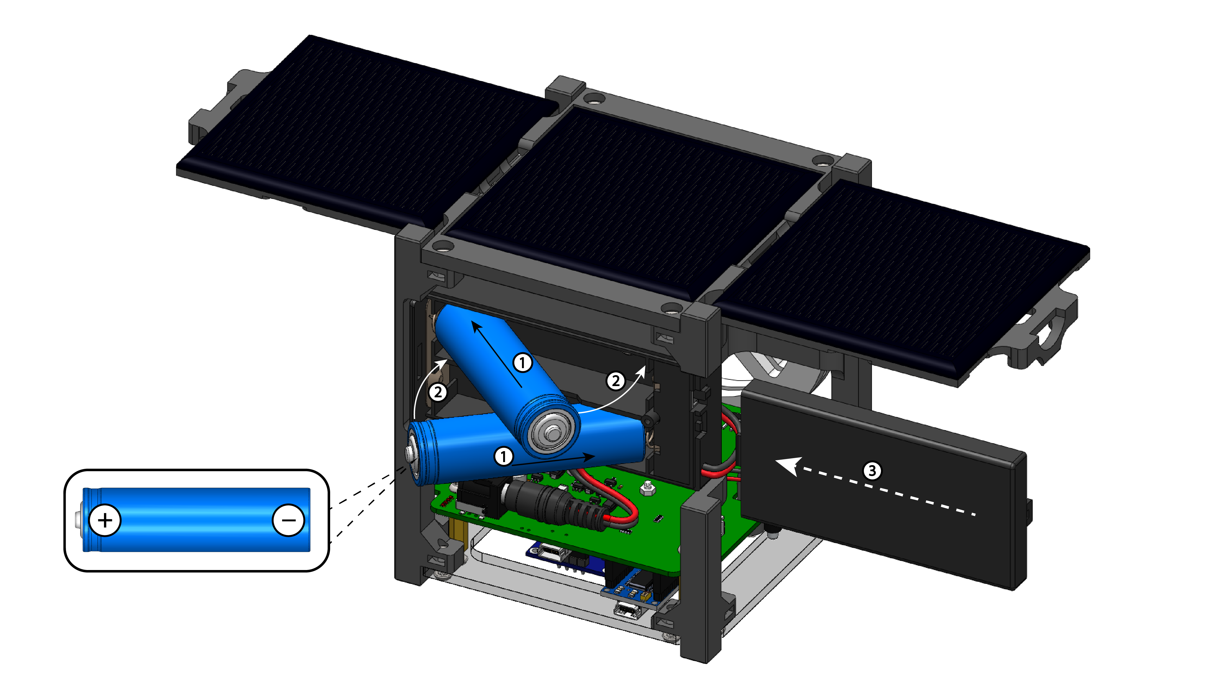
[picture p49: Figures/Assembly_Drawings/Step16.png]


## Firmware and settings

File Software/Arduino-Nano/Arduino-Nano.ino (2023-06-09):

#include <Wire.h>

#define SLAVE_ADDR             8
#define BATTERY_VOLTAGE_PIN   A0
#define SOLAR_VOLTAGE_PIN     A1
#define LIGHT_SENSOR1_PIN     A2
#define LIGHT_SENSOR2_PIN     A3
#define LIGHT_SENSOR3_PIN     A6
#define LIGHT_SENSOR4_PIN     A7
#define LED1_PIN               2
#define SERVO1_PIN             3
#define LED2_PIN               4
#define MOTOR_PWM1_PIN         5
#define MOTOR_PWM2_PIN         6
#define SOLENOID_PIN           7
#define LED3_PIN               8
#define SERVO2_PIN             9
#define SERVO3_PIN            10
#define SERVO4_PIN            11
#define LED4_PIN              12

unsigned long prev_t = 0;
unsigned long control_time = 50;  // run every ms 
unsigned long solenoid_t = 0;
const unsigned long solenoid_timer = 50; //500 // solenoid active duration
bool start_solenoid_timer = false;

byte battery_voltage_sensor = 0;
byte solar_voltage_sensor = 0;
byte light_sensor1 = 0;
byte light_sensor2 = 0;
byte light_sensor3 = 0;
byte light_sensor4 = 0;
bool motor_dir = true;
int motor_spd = 0;
bool is_deploy = false;
bool is_light_track = false;

void setup() {
  Serial.begin(115200);
  Wire.begin(SLAVE_ADDR); // join i2c bus with defined address
  Wire.onRequest(requestEvent); // trigger function when request by master
  Wire.onReceive(receiveEvent); // trigger function when data sent from master

  pinMode(SOLENOID_PIN,OUTPUT);
  pinMode(MOTOR_PWM1_PIN,OUTPUT);
  pinMode(MOTOR_PWM2_PIN,OUTPUT);
}

void loop() {
  unsigned long cur_t = millis();
  if (cur_t - prev_t >= control_time) {
    prev_t = cur_t;
    battery_voltage_sensor = map(analogRead(BATTERY_VOLTAGE_PIN),0,1023,0,255);
    solar_voltage_sensor = map(analogRead(SOLAR_VOLTAGE_PIN),0,1023,0,255);
    light_sensor1 = map(analogRead(LIGHT_SENSOR1_PIN),0,1023,0,255);
    light_sensor2 = map(analogRead(LIGHT_SENSOR2_PIN),0,1023,0,255);
    light_sensor3 = map(analogRead(LIGHT_SENSOR3_PIN),0,1023,0,255);
    light_sensor4 = map(analogRead(LIGHT_SENSOR4_PIN),0,1023,0,255);

    set_motor(motor_spd, motor_dir);

    if(is_deploy) {
      digitalWrite(SOLENOID_PIN,HIGH);
      if (!start_solenoid_timer) {
        Serial.println("Solenoid active");
        solenoid_t = cur_t;
        start_solenoid_timer = true;
      }
      if (start_solenoid_timer && cur_t - solenoid_t >= solenoid_timer) {
        digitalWrite(SOLENOID_PIN,LOW);
        Serial.println("Solenoid inactive");
        is_deploy = false;
        start_solenoid_timer = false;
      }
    } 

    if (is_light_track) {
      //TODO: function for students to implement
      byte light_left = max(light_sensor1,light_sensor4); //return max of 1/4
      byte light_right =  max(light_sensor2,light_sensor3); //return max of 2/3
      byte range = 50; //threshold to rotate the CubeSat
      byte track_speed = 80; //speed of rotate the CubeSat
      byte light_min = 80; // minimun light value to move
      if (light_left - light_right > range && light_left > light_min) { //if left side brighter
        set_motor(track_speed, 1); //turn left
      } else if (light_right - light_left > range && light_right > light_min) { //if right side brighter
        set_motor(track_speed, 0); //turn right
      } else {
        set_motor(0, 0); //stay
      }
    }

  }
}

void requestEvent() {
  Wire.write(battery_voltage_sensor);
  Wire.write(solar_voltage_sensor);
  Wire.write(light_sensor1);
  Wire.write(light_sensor2);
  Wire.write(light_sensor3);
  Wire.write(light_sensor4);
}

void receiveEvent(int howMany) {
  while (Wire.available() > 1) {
    char c = Wire.read();
    switch (c) {
      case '!':
        Serial.println("Deploy!");
        is_deploy = true;
        break;
      case '^':
        is_light_track = !is_light_track;
        if (!is_light_track) set_motor(0, 0);
        Serial.print("Light tracking: ");
        Serial.println(is_light_track ? "ON" : "OFF");
        break;
      case '+':
        motor_dir = true;
        Serial.print(c);
        break;
      case '-':
        motor_dir = false;
        Serial.print(c);
        break;
    } 
  }
  motor_spd = Wire.read();
  Serial.println(motor_spd);
}

void set_motor(int spd, bool dir) {
  if (spd == 0) { //stop
    digitalWrite(MOTOR_PWM1_PIN, LOW);
    digitalWrite(MOTOR_PWM2_PIN, LOW);
  } else if (dir) { //Clockwise
    digitalWrite(MOTOR_PWM1_PIN, LOW);
    analogWrite(MOTOR_PWM2_PIN, spd);
  } else if (!dir) { //Anticlockwise
    analogWrite(MOTOR_PWM1_PIN, spd);
    digitalWrite(MOTOR_PWM2_PIN, LOW);
  }
}

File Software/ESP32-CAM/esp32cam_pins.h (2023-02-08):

// camera pins for CAMERA_MODEL_AI_THINKER
#define PWDN_GPIO_NUM      32
#define RESET_GPIO_NUM     -1
#define XCLK_GPIO_NUM       0
#define SIOD_GPIO_NUM      26
#define SIOC_GPIO_NUM      27

#define Y9_GPIO_NUM        35
#define Y8_GPIO_NUM        34
#define Y7_GPIO_NUM        39
#define Y6_GPIO_NUM        36
#define Y5_GPIO_NUM        21
#define Y4_GPIO_NUM        19
#define Y3_GPIO_NUM        18
#define Y2_GPIO_NUM         5
#define VSYNC_GPIO_NUM     25
#define HREF_GPIO_NUM      23
#define PCLK_GPIO_NUM      22

// pins for peripherals
#define BUILDIN_LED_PIN     4
#define I2C_SDA            14 //I2C connect to 2 will cause flash fails
#define I2C_SCL            15
#define WIFI_RESET_TRIGGER 12 // Trigger pin for WIFI Configuration

// I2C address
#define SLAVE_ADDR          8

// channels for PWM
#define LED_CHN             7
//PWM configs
#define PWM_FREQ         2000
#define PWM_RES             8 //value:0-255

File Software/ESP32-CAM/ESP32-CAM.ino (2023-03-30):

/*
  OASA CubeSat with ESP32-CAM(ESP32 library V.1.0.6 required)
  Based upon Espressif ESP32-CAM Examples
  Author: Anson Mak
  
  ESP32 Board Library Version 1.0.6
  Library Requirement:
  - WiFiManager by Tzapu, tablatronix
  - Adafruit SSD1306 library
  - Adafruit GFX library
*/

#include "esp_wifi.h"
#include "esp_camera.h"
#include <WiFi.h>
#include <WiFiManager.h>
#include "esp32cam_pins.h"
#include "soc/soc.h"
#include "soc/rtc_cntl_reg.h"
#include "Wire.h"
#include <Adafruit_GFX.h> // Requires Adafruit GFX library
#include <Adafruit_SSD1306.h> // Requires Adafruit SSD1306 library

// AP Credentials
// const String CUBESAT_ID = "000";
// const String AP_SSID = "CubeSat" + CUBESAT_ID;
// const String AP_PW = "cubesat"+ CUBESAT_ID;

// Setup WiFi Access Point Credentials
// const char* ssid = "********";
// const char* password = "********";

unsigned long slave_prev_t = 0;
unsigned long slave_talk_time = 100; // time interval get data from slave
// received data from slave
int battery_voltage_sensor = 0;
float battery_voltage = 0.0;
float R1 = 10; //(k ohm) Resistance of R1
float R2 = 10; //(k ohm) Resistance of R2
float voltage_divider_constant = (R1+R2)/R2; // V_battery  = (R1+R2)/R2 * V_Measure 
const float voltage_offset = 0.15;
const float battery_min_voltage = 7.4;
const float battery_max_voltage = 8.2;
float battery_percentage = 0.0;
int solar_voltage_sensor = 0;
int light_sensor1 = 0;
int light_sensor2 = 0;
int light_sensor3 = 0;
int light_sensor4 = 0;

// data send to slave
extern bool send_slave;
extern bool is_deploy;
extern bool set_light_track;
extern byte motor_spd;
extern bool motor_dir;
extern bool is_flash;
bool start_led_flash_timer = false;
unsigned long led_flash_t = 0;
const unsigned long led_flash_timer = 500; //ms

#define SCREEN_WIDTH 128 // OLED display width, in pixels
#define SCREEN_HEIGHT 64 // OLED display height, in pixels
#define OLED_RESET -1 // Reset pin # (or -1 if sharing Arduino reset pin)
// Declaration for an SSD1306 display connected to I2C (SDA, SCL pins)
Adafruit_SSD1306 display(SCREEN_WIDTH, SCREEN_HEIGHT, &Wire, OLED_RESET);

void startCameraServer();
void led_blink();

void setup() {
  WRITE_PERI_REG(RTC_CNTL_BROWN_OUT_REG, 0); // disable brownout detector
  
  Serial.begin(115200);
  Serial.setDebugOutput(true);
  Serial.println();

  camera_config_t config;
  config.ledc_channel = LEDC_CHANNEL_0;
  config.ledc_timer = LEDC_TIMER_0;
  config.pin_d0 = Y2_GPIO_NUM;
  config.pin_d1 = Y3_GPIO_NUM;
  config.pin_d2 = Y4_GPIO_NUM;
  config.pin_d3 = Y5_GPIO_NUM;
  config.pin_d4 = Y6_GPIO_NUM;
  config.pin_d5 = Y7_GPIO_NUM;
  config.pin_d6 = Y8_GPIO_NUM;
  config.pin_d7 = Y9_GPIO_NUM;
  config.pin_xclk = XCLK_GPIO_NUM;
  config.pin_pclk = PCLK_GPIO_NUM;
  config.pin_vsync = VSYNC_GPIO_NUM;
  config.pin_href = HREF_GPIO_NUM;
  config.pin_sscb_sda = SIOD_GPIO_NUM;
  config.pin_sscb_scl = SIOC_GPIO_NUM;
  config.pin_pwdn = PWDN_GPIO_NUM;
  config.pin_reset = RESET_GPIO_NUM;
  config.xclk_freq_hz = 20000000;
  config.pixel_format = PIXFORMAT_JPEG;
  //init with high specs to pre-allocate larger buffers
  if(psramFound()){
    config.frame_size = FRAMESIZE_QVGA;
    config.jpeg_quality = 10;
    config.fb_count = 2;
  } else {
    config.frame_size = FRAMESIZE_QVGA;
    config.jpeg_quality = 12;
    config.fb_count = 1;
  }

  // camera init
  esp_err_t err = esp_camera_init(&config);
  if (err != ESP_OK) {
    Serial.printf("Camera init failed with error 0x%x", err);
    return;
  }

  //drop down frame size for higher initial frame rate
  sensor_t * s = esp_camera_sensor_get();
  s->set_framesize(s, (framesize_t)3);
  s->set_vflip(s, 1);
  s->set_hmirror(s, 1);
  s->set_quality(s, 35);
  

  // Set up pin for buildin led
  ledcSetup(LED_CHN, PWM_FREQ, PWM_RES);
  ledcAttachPin(BUILDIN_LED_PIN, LED_CHN);

  // Set up pin for triggering WIFI Configuration 
  pinMode(WIFI_RESET_TRIGGER, INPUT_PULLUP);

  // Set up I2C
  Wire.begin(I2C_SDA, I2C_SCL);
  
  // Set up OLED SSD1306 Connection
  if(!display.begin(SSD1306_SWITCHCAPVCC, 0x3C)) { // Address 0x3D for 128x64
    Serial.println(F("SSD1306 allocation failed"));
    for(;;);
  }
  delay(100);
  display.clearDisplay();
  display.setRotation(2); // rotate screen 180 degree
  display.setTextSize(1);
  display.setTextColor(WHITE);
  display.setCursor(0, 0);
  display.println("Searching WiFi...");
  display.display(); 
  delay(1000);

  // WiFi.begin(ssid, password);

  WiFiManager wfm;
  if (digitalRead(WIFI_RESET_TRIGGER) == LOW)
    wfm.resetSettings(); // erase saved credentials
  wfm.setAPCallback(configModeCallback); // call configModeCallback() when entered config WiFi mode
  // wfm.autoConnect(AP_SSID.c_str(),AP_PW.c_str()) //use define AP name and password
  if(!wfm.autoConnect()) { // auto generated AP name from chipID
      Serial.println("Failed to connect");
      // ESP.restart();
  }
  WiFi.setSleep(false);
  
  display.println("Saved SSID Found");
  display.print("WiFi Connecting");
  display.display(); 

  while (WiFi.status() != WL_CONNECTED) {
    delay(500);
    Serial.print(".");
    display.print(".");
    display.display(); 
    led_blink();
  }
  Serial.println("");
  Serial.println("WiFi connected");
  startCameraServer();

  Serial.print("Camera Ready! Use 'http://");
  Serial.print(WiFi.localIP());
  Serial.println("' to connect");

  // flash led
  led_multi_blink(5);
  
  // display connection message
  display.clearDisplay();
  display.setCursor(0, 0);
  display.println("Connected to: ");
  display.println(WiFi.SSID());
  display.println("");
  display.println("Control Panel IP:");
  display.println(WiFi.localIP());
  display.display(); 

  slave_prev_t = millis();
}
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

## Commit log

2022-08-13 Fixed battery voltage meter
    [app_httpd.cpp]
2022-08-16 Adjusted battery meter min max value
2022-09-01 Add MPU9250 for roll pitch yaw readings
2022-11-04 Minor IMU test
2022-11-04 Add OLED display for printing IP address
2022-11-30 add DRV8833 driver control
2022-12-06 Update motor pin assignment
2022-12-07 Add light sensor 3&4, remove imu data display
2022-12-10 Add button for stream rotation
2022-12-10 Change Slave motor PWM pin
2022-12-10 Test Esp32cam Button
2022-12-12 Add button for resetting SSID Credentials
    [esp32cam_pins.h]
2022-12-12 Add Stop Motor Button
2022-12-21 Add battery voltage divider equation
2023-02-08 Remove IMU(MPU9250) Stuff
2023-03-07 Add STL files
    [BottomPanel.STL, DeployLatchHole.STL, DeployPanel.STL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]
2023-03-08 Rename STL Files
    [10_Rail_mirror.STL, 11_Back_Panel.STL, 1_Deploy_Panel.STL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]
2023-03-09 Add 3DP Part List fig
    [8_Motor_Ring_Mount.STL]
2023-03-09 Add Assembly Instructions
2023-03-21 Remove Version1 STL
    [10_Rail_mirror.STL, 11_Back_Panel.STL, 1_Deploy_Panel.STL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]
2023-03-21 Add Version 2 STL
    [3DP_SpringLoadedHinge_1.STL, 3DP_SpringLoadedHinge_2.STL, BatteryBoxMount_bot.STL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]
2023-03-21 Add solar panel ADC
2023-03-21 Change motor control method
2023-03-25 Update V2 Assembly Instruction
2023-03-25 Update Assembly Fig
2023-03-30 Update battery voltage range
2023-03-30 Update CAD Fig
2023-05-06 Fix light sensor3 pin definition
    [Arduino-Nano.ino]
2023-05-25 Fix light_left & light_right definition
    [Arduino-Nano.ino]
2023-07-19 Update V2.1 Assembly Instruction
2023-07-21 Update STL
    [10_MotorBottomMount.STL, 11_MotorTopMount.STL, 12_Rail_c.STL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]
